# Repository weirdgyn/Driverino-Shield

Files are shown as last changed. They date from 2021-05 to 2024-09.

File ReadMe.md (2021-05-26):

# Driverino-Shield

### (italian noun) /ˈdraɪvərnəʊ/ : *little driver*

Driverino-Shield is a simple, low power, controller for [BLDC](https://en.wikipedia.org/wiki/Brushless_DC_electric_motor) sensored motors.
The aim of the project was to create an Arduino shield to drive PM BLDC motor(s) rated about 50-100W.
The board is designed around TI MCT8316Z BLDC chip: a very compact full featured driver that can be easily controlled from Arduino microcontroller.

PCB has been fully designed with KiCAD.

# TODO:

- [X] Submit to Made-With-KiCAD
- [ ] Add features:
   - [ ] encoder input.
   - [ ] current measurement (via INA250).
- [ ] Optimize PCB layout.
- [ ] Write Library.
   - [ ] Write Firmware.

# License

This project is released under CERN Open Hardware Licence Version 2 - Permissive.

# Links
* [This project on kitspace](https://kitspace.org/boards/github.com/weirdgyn/driverino-shield/)
* [TI MCT8316Z](https://www.ti.com/product/MCT8316Z?keyMatch=MCT8316Z&tisearch=search-everything)
* [Arduino](https://www.arduino.cc/)
* [KiCAD](https://www.kicad.org/)

#

Live long and prosper!

That's all folks.

By[t]e{s} Weirdgyn

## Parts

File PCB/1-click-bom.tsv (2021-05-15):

References | Qty | DNF | Manufacturer | Mouser | mpn
C1 | 1 |  | KEMET | 80-C1206C226M8R | C1206C226M8RACTU
C2 | 1 |  | Panasonic | 667-EEE-FKV121XSV | EEE-FKV121XSV
C3 | 1 |  | Taiyo Yuden | 963-GMK316AB7106KL | GMK316AB7106KL-TR
C4, C10, C11, C12 | 4 | 1 | TDK | 810-CGA3E2X7R1H104K | CGA3E2X7R1H104K080AA
C5, C7 | 2 |  | TDK | 810-C1608X7R1V105KAE | C1608X7R1V105K080AE
C6 | 1 |  | Murata | 81-GCM155R71H103KA5D | GCM155R71H103KA55D
C8, C9 | 2 |  | TDK | 10-CGA3E2X7R1H104K | CGA3E2X7R1H104K080AA
D1 | 1 |  | OSRAM Opto | 720-LOQ976-PS-25 | LO Q976-PS-25
D2 | 1 |  | OSRAM Opto | 720-LBQ39GN1P1351 | LB Q39G-N1OO-35-1
D3 | 1 |  | OSRAM Opto | 720-LTQ39GQ1S22515 | LT Q39G-Q1OO-25-1
D4 | 1 |  | OSRAM Opto | 720-LSQ976-NR-1 | LS Q976-NR-1
D5 | 1 |  | Taiwan Semiconductor | 821-TSZU52C5V1RGG | TSZU52C5V1 RGG
F1 | 1 |  | Bourns | 652-MF-NSMF020-2 | MF-NSMF020-2
JP1 | 1 |  | Samtec | 200-TMS10301GS | TMS-103-01-G-S
JP2 | 1 |  | Samtec | 200-TMS10201GS | TMS-102-01-G-S
L1 | 1 |  | Taiyo Yuden | 963-CBC3225T470KRV | CBC3225T470KRV
P1 | 1 |  | Samtec | 200-SSW10803GS | SSW-108-03-G-S
P2 | 1 |  | Samtec | 200-SSW10603GS | SSW-106-03-G-S
P3 | 1 |  | Samtec | 200-SSW11003GS | SSW-110-03-G-S
P4 | 1 |  | Samtec | 200-SSW10803GS | SSW-108-03-G-S
P5, P6, P7, P8 | 4 | 1
P9 | 1 |  | Molex | 538-39773-0002 | 39773-0002
P10 | 1 |  | Molex | 538-39773-0003 | 39773-0003
P11 | 1 |  | Molex | 538-53047-0810 | 53047-0810
R1, R3, R5, R13 | 4 |  | Vishay | 71-CRCW06031K00FKEAC | CRCW06031K00FKEAC
R2, R4, R6 | 3 |  | Rohm | 755-ESR03EZPF5101 | ESR03EZPF5101
R7 | 1 |  | Panasonic | 667-ERJ-3RBD6202V | ERJ3RBD6202V
R8 | 1 |  | Yageo | 603-RC0603FR-0710KL | RC0603FR-0710KL
R9, R10, R11, R12, R14, R15, R16, R17 | 8 |  | Vishay | 71-CRCW06030000Z0EBC | CRCW06030000Z0EBC
R18, R19, R20, R21, R22, R23 | 6 | 1 | Vishay | 71-CRCW040210K0JNEDC | CRCW040210K0JNEDC
U1 | 1 |  | TI |  | PMCT8316Z0TRGFR

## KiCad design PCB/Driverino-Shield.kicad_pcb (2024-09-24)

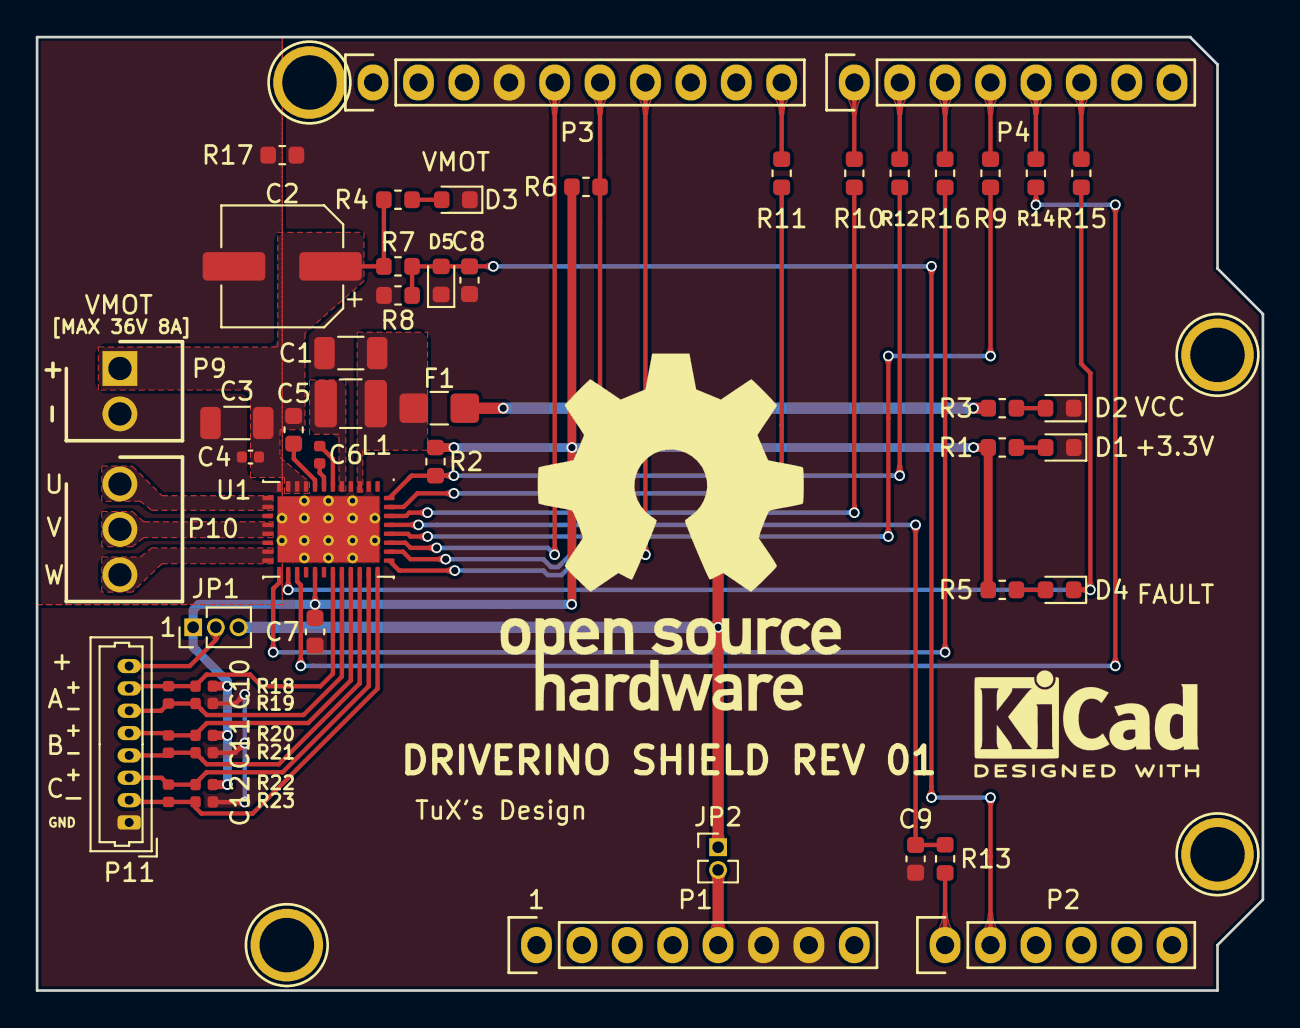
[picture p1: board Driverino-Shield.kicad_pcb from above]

Board: 2 copper layers, 68.6 x 53.3 mm, 56 parts (0 on the bottom side), 47 nets.

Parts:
C1: 22uF; C_1206_3216Metric
C2: 150uF; CP_Elec_6.3x7.7
C3: 10uF; C_1206_3216Metric
C4, C10, C11, C12: 100nF; C_0402_1005Metric
C5, C7: 1uF; C_0603_1608Metric
C6: 10nF; C_0402_1005Metric
C8, C9: 100nF; C_0603_1608Metric
D1: ORANGE; LED_0603_1608Metric
D2, D4: BLUE; LED_0603_1608Metric
D3: GREEN; LED_0603_1608Metric
D5: Vz=5V; D_0603_1608Metric
F1: 200mA; Fuse_1206_3216Metric_Castellated
JP1: HAL_SEL; PinHeader_1x03_P1.27mm_Vertical
JP2: VCC_SEL; PinHeader_1x02_P1.27mm_Vertical
L1: 47uH; L_1210_3225Metric
P1: Power; Socket_Strip_Arduino_1x08
P2: Analog; Socket_Strip_Arduino_1x06
P3: Digital; Socket_Strip_Arduino_1x10
P4: Digital; Socket_Strip_Arduino_1x08
P5, P6, P7, P8: CONN_01X01; Arduino_1pin
P9: PWR; 39773-0002
P10: MOT; 39773-0003
P11: HALL; Molex_PicoBlade_53047-0810_1x08_P1.25mm_Vertical
R1, R3, R5, R7, R8, R13: 1k; R_0603_1608Metric
R2, R6: 5.1k; R_0603_1608Metric
R4: 4.7k; R_0603_1608Metric
R9, R10, R11, R12, R14, R15, R16, R17: 0R; R_0603_1608Metric
R18, R20, R22: 10k; R_0402_1005Metric
R19, R21, R23: 0R; R_0402_1005Metric
U1: MCT8316Z; QFN-40_EP_5x7_Pitch0.5mm

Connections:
+3.3V: C7.1, JP1.1, P1.4, R1.1, R2.1, R5.1, R6.1, R18.2, R20.2, R22.2, U1.25
+5V: JP2.2, P1.5
+36V: C2.1, C3.2, C4.2, C5.2, P9.1, R4.1, R7.2, U1.9, U1.10, U1.11
/2: P4.6, R15.1
/3(**): P4.5, R14.1
/4: P4.4, R9.1
/5(**): P4.3, R16.1
/6(**): P4.2, R12.1
/7: P4.1, R10.1
/8: P3.10, R11.1
/11(**/MOSI): P3.7, U1.34
/12(MISO): P3.6, R6.2, U1.33
/13(SCK): P3.5, U1.35
/A0: P2.1, R13.2
/A1: C8.2, D5.2, P2.2, R7.1, R8.1
/A4(SDA): P2.5, P3.2
/A5(SCL): P2.6, P3.1
/BRAKE: R10.2, U1.38
/CS: R9.2, U1.36
/DRVOFF: R16.2, U1.21
/FAULT: D4.1, R15.2, U1.22
/FB: C1.2, F1.2, L1.1, U1.3
/FGOUT: R2.2, R12.2, U1.40
/HAN: C10.1, P11.6, R19.1, U1.28
/HAP: C10.2, P11.7, R18.1, U1.27
/HBN: C11.1, P11.4, R21.1, U1.30
/HBP: C11.2, P11.5, R20.1, U1.29
/HCN: C12.1, P11.2, R23.1, U1.32
/HCP: C12.2, P11.3, R22.1, U1.31
/ILIM: C9.2, R13.1, U1.37
/PWM: R11.2, U1.39
/SLEEP: R14.2, U1.23
/SW: L1.2, U1.5
/U: P10.1, U1.13, U1.14
/V: P10.2, U1.16, U1.17
/W: P10.3, U1.19, U1.20
GND: C1.1, C7.2, C8.1, C9.1, D1.1, D2.1, D3.1, D5.1, P1.6, P1.7, P3.4, P11.1, R8.2, R17.2, R19.2, R21.2, R23.2, U1.2, U1.4, U1.41
GNDPWR: C2.2, C3.1, C4.1, P9.2, R17.1, U1.12, U1.15, U1.18
unnamed: C5.1, U1.8
unnamed: C6.1, U1.7
unnamed: C6.2, U1.6
unnamed: D1.2, R1.2
unnamed: D2.2, R3.2
unnamed: D3.2, R4.2
unnamed: D4.2, R5.2
unnamed: JP1.2, P11.8
VCC: F1.1, JP1.3, JP2.1, R3.1

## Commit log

2021-05-10 Routing completed
    [Driverino-Shield.kicad_pcb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]
2021-05-10 Update gerbers
    [Driverino-Shield-B_Cu.gbr, Driverino-Shield-B_Mask.gbr, Driverino-Shield-B_Paste.gbr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]
2021-05-10 .tsv file generated
    [1-click-bom.tsv, Driverino-Shield.sch]
2021-05-11 Add kitspace.yaml, rename gerber folder
    [Driverino-Shield-B_Cu.gbr, Driverino-Shield-B_Mask.gbr, Driverino-Shield-B_Paste.gbr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]
2021-05-11 Update BOM
    [1-click-bom.tsv, Driverino-Shield.sch]
2021-05-11 BOM Update
    [1-click-bom.tsv, Driverino-Shield.sch]
2021-05-11 Updated .gitignore
    [Driverino-Shield.xlsx]
2021-05-11 .gitignore update, made-with-kicad logo
    [Driverino-Shield.kicad_pcb, Driverino-Shield.xlsx]
2021-05-11 Updated BOM
    [1-click-bom.tsv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]
2021-05-12 Fixed VMOT input resistance partition, update BOM
    [1-click-bom.csv, Driverino-Shield.sch]
2021-05-12 Changed F1 footprint, BOM update
    [1-click-bom.csv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]
2021-05-13 Update directory tree
    [1-click-bom.csv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]
2021-05-13 Add teardrops
    [Driverino-Shield-B_Cu.gbr, Driverino-Shield-B_Mask.gbr, Driverino-Shield-B_Paste.gbr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]
2021-05-13 Update BOM
    Revert on .tsv
    [1-click-bom.csv, 1-click-bom.tsv]
2024-09-24 Update to KiCAD version 8.0
    [Driverino-Shield.kicad_pcb, Driverino-Shield.kicad_sch, Driverino-Shield.sch]

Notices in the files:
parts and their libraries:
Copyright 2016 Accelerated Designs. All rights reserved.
